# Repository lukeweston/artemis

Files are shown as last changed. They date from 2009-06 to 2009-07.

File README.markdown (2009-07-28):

ARTEMIS: Arduino Rocket Telemetry Module and Instrumentation System
===================================================================

*more documentation to come later*

Hardware
--------

(I'm having some trouble learning how to make the markdown code block work properly...
...please bear with me here.)

                Hardware Arduino pin assignments:
    
                Function                                Mega pin                Duemilanove pin 
    
                UART Rx from XBee:                      Digital 0 (RX0)         (0) 
                UART Tx to XBee:                        Digital 1 (TX0)         (1) 
                1-Wire (DS18B20)                        Digital 2               (2) 
                Accelerometer (ADXL330) self-test       Digital 3               (3) 
    
                LDR 1:                                  Analog 0                (Analog 0)
                LDR 2:                                  Analog 1                (Analog 1)
                Battery voltage:                        Analog 7
    
                UART Tx to GPS module:                  18 (TX1)
                UART Rx from GPS module:                19 (RX1)
    
                I2C serial data for DS1307 RTC:         20 (SDA)
                I2C clock:                              21 (SCL)
    
                Atmel DataFlash SPI chip select:        46  
                MCP3204 ADC (5 V) SPI chip select:      47  
                MCP3208 ADC (3.3 V) SPI chip select:    48  
    
                SPI Master-in-slave-out (MISO):         50  
                SPI Master-out-slave-in (MOSI):         51  
                SPI clock (SCK):                        52  

(Note that pins 20, 21, 50 51 and 52 are hard-wired to the microcontroller's
internal hardware for those interface protocols, and cannot be changed.)

Although it is designed to be used with an Arduino Mega, some pins (The DS18B20, the LDRs and 
the XBee module) can be tested with the board plugged into an Arduino Duemilanove.

On future PCBs it would be nice to change the battery voltage measurement input from Analog 7 to Analog 5,
to allow this function to be tested on an Arduino Duemilanove. This was just a little bit of laziness on the 
part of the PCB designer, since pin 7 is the one closest to that part of the layout.

*The accelerometer self-test should be used with caution* since it is plugged straight into the microcontroller
and the accelerometer is a 3.3V device. Perhaps PWMing it would be appropriate - I should have added a capacitor
on this pin on the board to smooth off the PWM.

Software
--------

Clone this into your Arduino projects directory (~/Documents/Arduino on the Mac), and you should be able to open it in your Arduino IDE, build it, and run it.

The following bits are working:

- ADCs
- Accelerometer
- MAP sensor
- Real-time clock
- Temperature

The following bits still need to be done:

- Flash storage
- GPS

From there we have to work out formats for data storage and transmission.

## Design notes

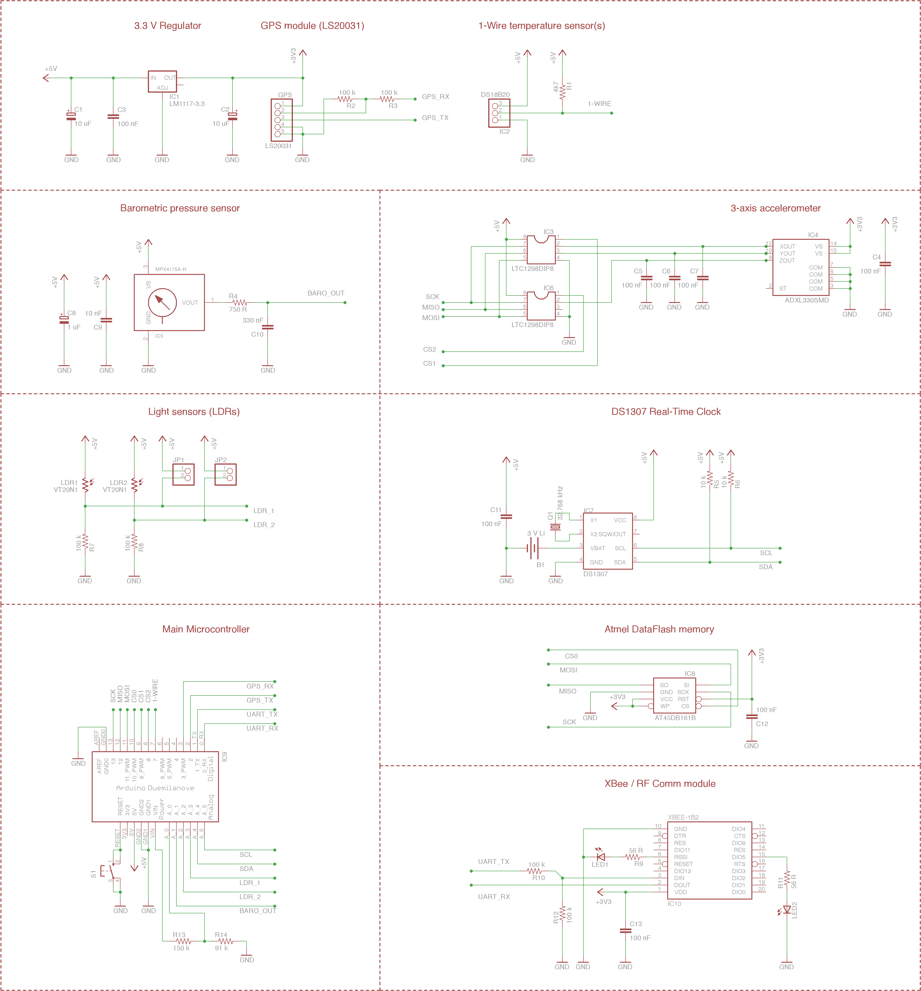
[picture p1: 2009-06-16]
hardware/artemis-schematic.png

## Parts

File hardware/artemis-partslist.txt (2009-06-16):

Resistors: (All resistors 0805 SMD package)

R1	4.7 k
R2	100 k
R3	100 k
R4	750 R
R5	10 k
R6	10 k
R7	100 k
R8	100 k
R9	56 R
R10	100 k
R11	56 R
R12	100 k
R13	150 k
R14	91 k

Capacitors:

C1	10 uF 16 V tantalum, through-hole					Jaycar RZ-6648 
C2	10 uF 16 V tantalum, through-hole					Jaycar RZ-6648
C3	100 nF, 0805 SMD package
C4	100 nF, 0805 SMD package
C5	100 nF, 0805 SMD package
C6	100 nF, 0805 SMD package
C7	100 nF, 0805 SMD package
C8	1 uF, 25 V tantalum, through-hole					Jaycar RZ-6627
C9	10 nF, 0805 SMD package
C10	330 nF, 0805 SMD package
C11	100 nF, 0805 SMD package
C12	100 nF, 0805 SMD package
C13	100 nF, 0805 SMD package

ICs:

	I've specified some examples of parts suppliers that I know have the relevant items, though they may not be the only choices, or the best choices.

IC1	Linear LM1117-3.3 LDO 3.3 V voltage regulator, SOT-223 package		Digikey LM1117MP-3.3CT-ND
IC2	Dallas DS18B20 1-Wire temperature sensor, TO-92 package			Sparkfun SEN-00245
IC3	Linear LTC1298 analog-to-digital converter, DIP-8 package		Futurelec
IC4	Analog Devices ADXL330 3-axis accelerometer, LFCSP-16 package		Sparkfun COM-00730
IC5	Freescale MPX4115A barometric pressure sensor, 867-H package		Digikey
IC6	Linear LTC1298 analog-to-digital converter, DIP-8 package		Futurelec
IC7	Dallas DS1307 real-time clock, SOIC-8 package				Futurelec
IC8	Atmel AT45DB161B 16 MBit DataFlash memory, SOIC-8 package		Sparkfun COM-00301

IC9	Arduino Duemilanove board
IC10	XBee module (any, really)
GPS	LS20031 GPS module							Sparkfun GPS-08975

B1	12 mm coin cell holder, SMD						Sparkfun PRT-07948
	plus CR1225 3 V lithium coin cell					Sparkfun PRT-00337
Q1	32.768 kHz quartz oscillator crystal, TC-38 through-hole package	Sparkfun COM-00540
S1	Momentary tactile pushbutton switch, through-hole			Jaycar SP-0600
LDR1	Standard cadmium sulfide photoresistor, through-hole 0.1"		Jaycar RD-3480
LDR2	Standard cadmium sulfide photoresistor, through-hole 0.1"		Jaycar RD-3480
LED1	Standard LED; 3 mm through-hole						Jaycar ZD-0120
LED2	Standard LED; 3 mm through-hole						Jaycar ZD-0120

2 x 10-pin 2 mm header sockets for XBee module					Sparkfun PRT-08272
Break-away 0.1" machined pin socket strip for mounting LTC1298 ICs		Jaycar PI-6470
28-pin break-away 0.1" pin header strip for mounting shield to Arduino		Jaycar HM-3211

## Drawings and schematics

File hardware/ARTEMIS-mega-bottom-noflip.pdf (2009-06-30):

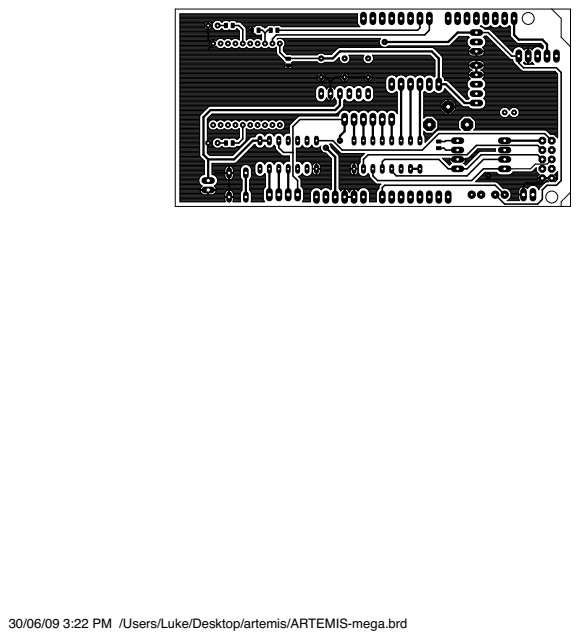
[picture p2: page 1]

30/06/09 3:22 PM /Users/Luke/Desktop/artemis/ARTEMIS-mega.brd

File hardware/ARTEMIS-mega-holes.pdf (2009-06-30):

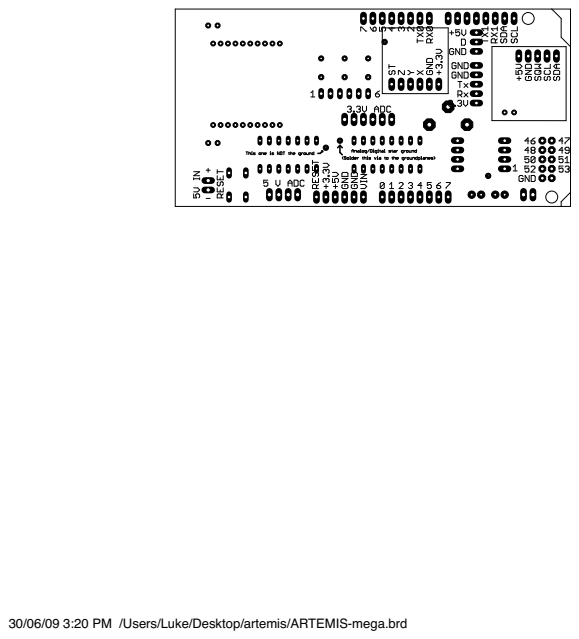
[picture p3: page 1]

30/06/09 3:20 PM /Users/Luke/Desktop/artemis/ARTEMIS-mega.brd

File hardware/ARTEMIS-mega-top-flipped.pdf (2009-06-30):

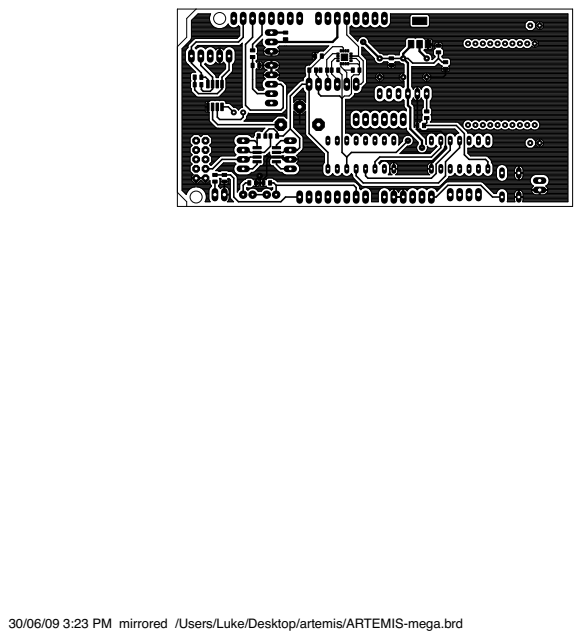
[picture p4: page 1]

30/06/09 3:23 PM mirrored /Users/Luke/Desktop/artemis/ARTEMIS-mega.brd

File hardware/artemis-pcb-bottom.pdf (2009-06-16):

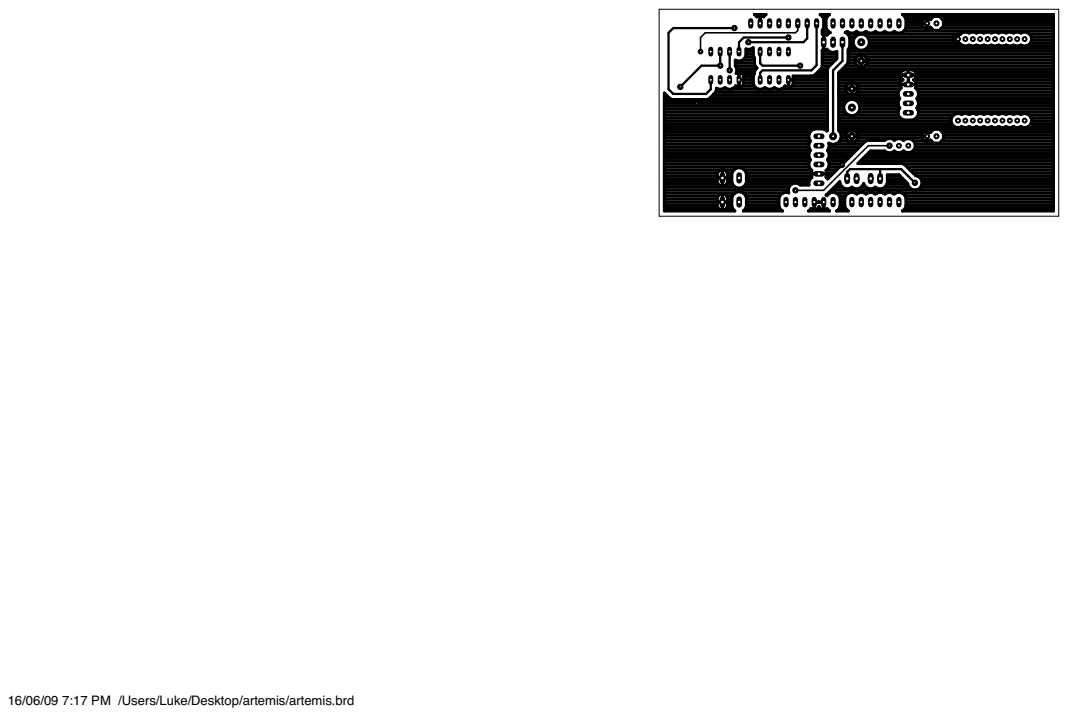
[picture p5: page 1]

16/06/09 7:17 PM /Users/Luke/Desktop/artemis/artemis.brd

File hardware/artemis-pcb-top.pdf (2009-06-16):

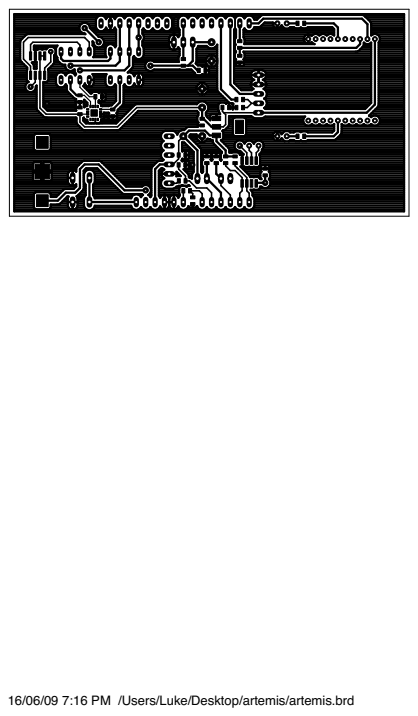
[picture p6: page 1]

16/06/09 7:16 PM /Users/Luke/Desktop/artemis/artemis.brd

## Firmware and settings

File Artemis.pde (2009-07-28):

#include <AikoDeviceMCP320x.h>
#include <AikoEvents.h>
#include <Wire.h>
#include <OneWire.h>
#include "ADXL330.h"
#include "DS1307.h"
#include "DS18B20.h"
#include "MPX4101A.h"

using namespace Aiko;

Device::MCP320x   adc5v(47);
Device::MCP320x   adc3v(48);
ADXL330           accelerometer(adc3v);
MPX4101A          mapSensor(adc5v);
DS1307            clock;
OneWire           oneWire(2);
DS18B20           temperatureSensor(oneWire);

void reportNodeName() {
  Serial.println("(nodeName= artemis_1)");
}

void readClock() {
  clock.read();
  
  Serial.print("(clock= ");
  if (clock.hour_ < 10) Serial.print('0');
  Serial.print((int)clock.hour_);
  if (clock.minute_ < 10) Serial.print('0');
  Serial.print((int)clock.minute_);
  if (clock.second_ < 10) Serial.print('0');
  Serial.print((int)clock.second_);
  Serial.println(")");
}

void readAccelerometer() {
  int x = accelerometer.readX();
  int y = accelerometer.readY();
  int z = accelerometer.readZ();
  
  Serial.print("(acceleromter_x= ");
  Serial.print(x);
  Serial.println(")");
  
  Serial.print("(acceleromter_y= ");
  Serial.print(y);
  Serial.println(")");
  
  Serial.print("(acceleromter_z= ");
  Serial.print(z);
  Serial.println(")");
}

void readMapSensor() {
  Serial.print("(barometer= ");
  Serial.print(mapSensor.readPressure());
  Serial.println(")");
}

void readLDRs() {
  Serial.print("(light_a= ");
  Serial.print(analogRead(0));
  Serial.println(")");
  Serial.print("(light_b= ");
  Serial.print(analogRead(1));
  Serial.println(")");
}

void readVoltage() {
  float voltage = (float)analogRead(7) * (5.0 / 1024.0);
  
  Serial.print("(voltage= ");
  Serial.print(voltage);
  Serial.println(")");
}

void readTemperature() {
  temperatureSensor.read();
  
  Serial.print("(temperature= ");
  Serial.print(temperatureSensor.temperature());
  Serial.println(")");
  
  temperatureSensor.startConversion();
}

void setup() {
  clock.second_ = 0;
  clock.minute_ = 1;
  clock.hour_   = 2;
  clock.dayOfWeek_ = 3;
  clock.dayOfMonth_ = 4;
  clock.month_ = 5;
  clock.year_ = 6;
  clock.set();
  
  Serial.begin(9600);
  Events.addHandler(reportNodeName, 1000);
  Events.addHandler(readClock, 1000);
  Events.addHandler(readAccelerometer, 100);
  Events.addHandler(readMapSensor, 100);
  Events.addHandler(readLDRs, 100);
  Events.addHandler(readVoltage, 100);
  Events.addHandler(readTemperature, 1000);
}

void loop() {
  Events.loop();
}

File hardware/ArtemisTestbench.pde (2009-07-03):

/*  Some simple test code for the ARTEMIS board, to take the temperature measurement from the DS18B20 sensor as well
    as the analog reading of the light level from the two LDRs, and display the values from these sensors on the
    serial terminal, as a simple test to confirm that the board, or at least these sensors, are working at the
    hardware level.
    
    This code was developed, and works, with the ARTEMIS board plugged into an Arduino Duemilanove, not an
    Arduino Mega. However, it's simply a matter of knowing the appropriate pin numbers to use.
    
    This simple code borrows heavily from the example code supplied for the DallasTemperature library by Miles Burton,
    as available on the Arduino Playground page.
*/

#include <DallasTemperature.h>

DallasTemperature tempSensor;

void setup(void) {
  // initialize devices
  Serial.begin(9600);   // start serial port
  tempSensor.begin(2); // The ARTEMIS board, plugged into an Arduino Duemilanove, brings the 1-Wire bus to pin 2.                        
}

void loop(void) {

    // Ask the library whether the device is valid
    switch(tempSensor.isValid())
    {
        case 1:
            Serial.println("Invalid CRC");
			tempSensor.reset(); // Attempts to redetect IC
            return;
        case 2:
            Serial.println("Not a valid device");
			tempSensor.reset();
            return;
    }

  Serial.print("Temperature: ");
  Serial.print(tempSensor.getTemperature());
  Serial.print(" C");
  Serial.println();
  
  Serial.print("LDR 1: ");
  Serial.print(analogRead(0));
  Serial.print("/1024");
  Serial.println();
  
  Serial.print("LDR 2: ");
  Serial.print(analogRead(1));
  Serial.print("/1024");
  Serial.println("\n");
 
  delay(1000);
  
}

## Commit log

2009-06-16 actually uploaded some content
    [artemis.brd, artemis.sch]
2009-06-16 Version 0.1
    [artemis.brd]
2009-06-30 Complete design for Mega shield for ARTEMIS
    [ARTEMIS-mega.brd, ARTEMIS-mega.sch]
2009-07-03 Added "testbench" Arduino code for DS18B20 and LDR
2009-07-04 Added README.markdown with Arduino pin assignments
2009-07-28 Pulled in the Artemis software.
    [ARTEMIS-mega.brd, ARTEMIS-mega.sch, artemis.brd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]
